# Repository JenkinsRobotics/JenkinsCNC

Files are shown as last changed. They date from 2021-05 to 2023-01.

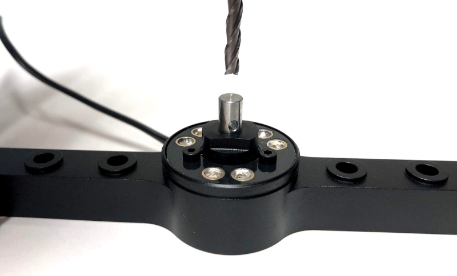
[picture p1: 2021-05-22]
CODE/SDCARD/www/img/touchplate.201649f8.png

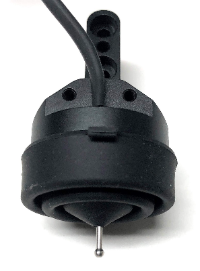
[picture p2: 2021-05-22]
CODE/SDCARD/www/img/probe.2c0976e9.png

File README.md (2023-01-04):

## Jenkins Robotics
# Jenkins CNC Project Files
<!-- This is commented out. -->

## Project Information

Project Status : <mark style="background-color: green"> &nbsp; COMPLETED &nbsp;</mark>  
Code Status : <mark style="background-color: green"> &nbsp; GOOD &nbsp;</mark>  
Development Status : <mark style="background-color: red"> &nbsp; NOT ACTIVE &nbsp;</mark>  

&nbsp;
## General Information

 This is the project files for our Shapeoko 3 xxl. Our goal is to make our shapeoko 3 as automated as possible. To achive this goal we have installed multiple upgrades onto our cnc including: 
- [x] Duet 3 Control Board
- [x] Pnumatic tool changer
- [x] Varible Fequency Drive & spindle
- [x] Tool TCP Probe
- [x] Work Piece XYZ Probe
- [x] Custum Fusion 360 Post Processor
- [x] Pnumatic Dust Shoe

&nbsp;
## WATCH NOW ON YOUTUBE

 Watch the project playlist on youtube. 

 &nbsp;

image alt text (https://youtube.com/playlist?list=PLNTKXZ4hgP_jekZOWw05JcJtyseCdSsIV "YouTube")

&nbsp;
## Support

Did this project help you? Consider supporting! 

Consider Subscribing: https://bit.ly/2DgZyuq <br>
Patreon ➔ https://www.patreon.com/JenkinsRobotics <br>
Venmo ➔ https://venmo.com/u/JenkinsRobotics <br>

&nbsp;
## Table of Contents

**[Project File Structure](#project-file-structure)**<br>
**[Installation Instructions](#installation-instructions)**<br>
**[Next Steps](#next-steps)**<br>
**[Components](#components)**<br>
**[Notes and Miscellaneous](#notes-and-miscellaneous)**<br>
**[Links](#links)**<br>

&nbsp;
## Project File Structure

The following is a breakdown of the different folders and the files contained in them:

1. **CAD**
   - *Online Models*
    Reference CAD models were used in the modeling of the shapeoko 360. Including a generic Shapeoko 3 model and a Duet 3 Model. We are also using a generic CAD cover for the LCD screen that can be downloaded directly from thingiverse. All reference CAD models used are copied here with any other documentation and licenses that came with the file. 

   - *Jenkins Robotics CAD*
    All released CAD models will be posted here on Github. Every CAD model made by us are given a part number (JRCNC###). Original files are created using fusion 360. Most files will also be given proper engineering drawings once a release version of the file is posted.
    
    &nbsp;
2. **CODE**  
   - *SDCARD*
    This folder contains a copy of all they files located on our Duet 3 Motherboard SD Card. The system drive contains multiple subfolders each containing different gcode / system files. Before Copying/referencing our  custom files it is best to upgrade the stock firmware and system files. The official Duet 3 releases can be found on GitHub.  [RepRap Files](https://github.com/Duet3D "Duet3D").
      
   - *Macros*
    The Macro folder contains all the additional system files needed for the Duet 3. Files are grouped by their function. 
     **Directions:**
        - Upload any of the desired files. Then review the files and make any necessary  adjustment to the position points and the probe/sensors numbers.  

   - *Sys*
    The System folder contains all the important system files needed for the Duet 3. Each file serves as important gcode files that configures the machine and provide necessary gcode for specific processes like tool changes. 
        **Directions:**
        - Upload the following files: Config*, TFree, Tpost, Tpre, Zprobe, Lighthome, lighton. 
        - Config file is specific to each machine. and will require modification based on the wiring of your specific machine. Use our config file and our wire diagram as reference. 
        - The TFree/Tpost/Tpre and ZProbe are all required files to add support for ATC and Automatic Tool offset probe. Copy these files and adjust the position data as necessary. 

    &nbsp;
3. **DIAGRAMS**
   - *Jenkinc CNC Wire Diagram (JRCNCWD1)*
    A wiring diagram is a simplified conventional pictorial representation of an electrical circuit. It shows the components of the circuit as simplified shapes, and the power and signal connections between the devices Reference the wire diagram to review how each electrical component is connected to the Duet board

   - *Duet 3 Reference files*
    Reference files are used to highlight specific information that useful for the operation, installation of the duet board.  Duet3D online wiki contains many more useful information and [Documentations](https://duet3d.dozuki.com/ "Duet3D").
  
    &nbsp;
4. **FUSION 360 POST PROCESSOR**
     
   - *JenkinsCNCReprap.cps*
    A post processor is the link between the CAM system and your CNC machine. The Post Processor translated the CAM instruction including information like the toolpath data, the type of operation, and the desired spindle feeds/speeds into the language that a CNC machine understands (gcode). Despite the fact that the DUET 3 runs RepRap Firmware, the standard RepRap post processor do not work for CNC machining. Our Custom post processor is based on the default RepRap post processor but fixes the gcode syntax errors and adds  Automatic Tool Change / Spindle Controls support. 
    **Directions:**
      - Uploading file to Fusion 360 Cloud Storage [Personal-cloud]
        With-in Fusion 360 open the project navigation panel. Under Libraries select "Assets", then select folder "CAMPosts" (if no folder exist then create one.) Upload the custom Post Processor within this folder for cloud storage. 
      - Create NC Program
        After creating your CAD model select the "Manufacturing Tab" in Fusion 360. Complete the "Setup" process and the desired toolpaths. Create a new "NC Program".  Under "Post Configuration / Library" specify the location of the Post Processor File [personal-cloud recommended]. Under Post specify the desired file "Jenkins CNC RepRap". Adjust Post Properties if desired, then export gcode.  

    &nbsp;
5. **MANUALS**
   - *Reference Materials*
    The manuals folder contains reference material for different hadware apart of the CNC. 
      - The VFD Manual contains the custom settings specific for our spindle.
      - Automatic Tool Changer (ATC) manual contains information required to "run-in" a new spindle to properly prepare it before running production

> Note: Updating the RepRap firmware should be done carefully. Uploading the updated ZIP file could erase custom gcode files. 

&nbsp;
## Installation Instructions

Installation instructions can be found in the youtube video linked below 

 ### Video link  be updated soon

image alt text (https://youtube.com/playlist?list=PLNTKXZ4hgP_jekZOWw05JcJtyseCdSsIV "YouTube")

<!-- This is commented out.  

The following is a breakdown of the different folders and the files contained in them:

```
cd utils
node build.js
```

Create a file with a `.zip` extension containing these files and directories:

```
manifest.json
common/
chrome/
```

Create a file with a `.xpi` extension containing these files and directories:

```
chrome.manifest
install.rdf
common/
firefox/
```

 This is commented out. -->

&nbsp;
## Next Steps

This project is now completed. No next steps are planned. We can release bug fixes if found. 

If you require assistant join our discord channel linked down below.

&nbsp;
## Components 

The following is a breakdown of key components for this project:
&nbsp;
| Item | Function | Cost  | Link  |
| --- |:---:| -----:|-----:|
| Fusion 360 | CAD | Free | Free |
| VS Code | Text Editor | Free | Free |
| Spindle | Spindle  | $220 | (https://www.amazon.com/dp/B088824MPT/...) |
| Tool Changer for Water or Air Cooled Spindle 0.8 or 1.5KW 65mm | ATC | $400 | (https://cnccat.com/index.php?id=2&productid=1964&catid=0&subcatid=&lang=en) |

&nbsp;
## Notes and Miscellaneous

Disclaimer :
Modifying your Shapeoko  will void the warranty. Do at your own risk.

**ENJOY!!**

That’s  all Folks. Hope this can help you in some way.
... Consider Supporting Us Down Below. 

&nbsp;
## Links

SUPPORT US ► 

Consider Subscribing: https://bit.ly/2DgZyuq <br>
Patreon ➔ https://www.patreon.com/JenkinsRobotics  <br>
Venmo ➔ https://venmo.com/u/JenkinsRobotics <br>

FOLLOW US ►

Discord ➔ https://discord.gg/sAnE5pRVyT <br>
Patreon ➔ https://www.patreon.com/JenkinsRobotics <br>
Twitter ➔ https://twitter.com/j <br>
Instagram  ➔ https://www.instagram.com/jenkinsrobotics/ <br>
Facebook ➔ https://www.facebook.com/jenkinsrobotics/  <br>
GitHub  ➔ https://jenkinsrobotics.github.io <br>

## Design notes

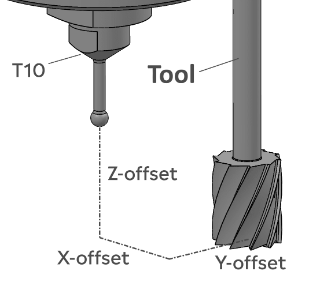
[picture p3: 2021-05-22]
CODE/SDCARD/www/img/tooloffset.c75178cf 2.png

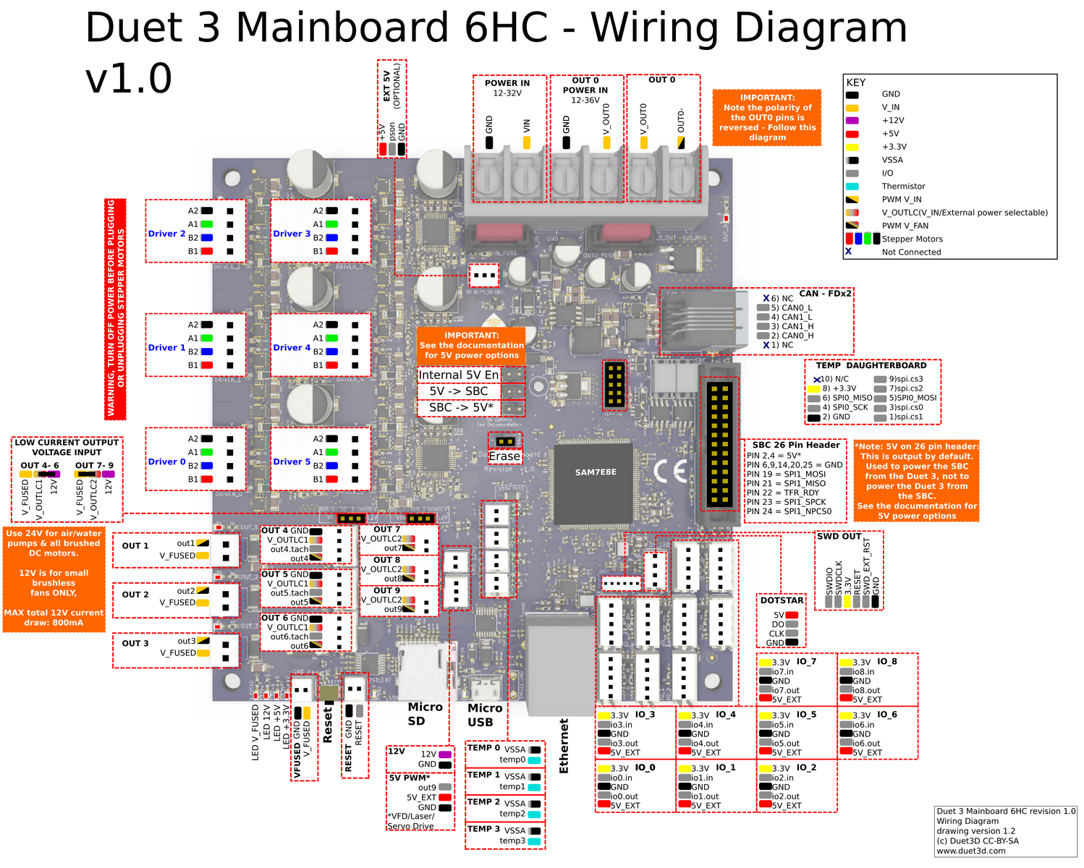
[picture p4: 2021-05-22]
DIAGRAMS/DUET 3 Diagram.jpg

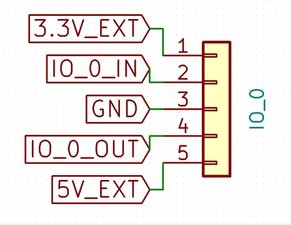
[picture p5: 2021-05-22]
DIAGRAMS/Duet 3 IO port.jpg

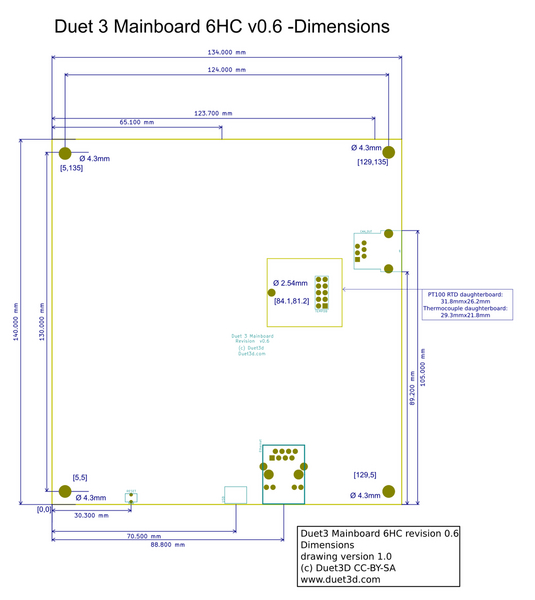
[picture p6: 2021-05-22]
DIAGRAMS/DUET 3 BOARD SIZE.jpg

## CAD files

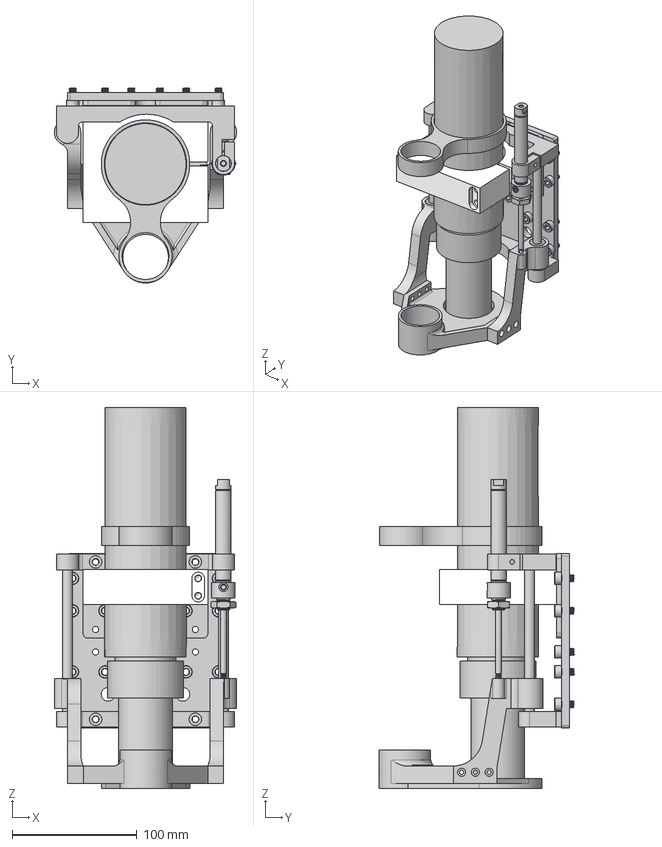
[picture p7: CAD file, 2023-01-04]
CAD/JR ASSEMBLIES/shapeoko Z Axis Upgrades v40.step
146.3 x 156.4 x 305.5 mm
91290A316 x 14
Shapeoko3_Spindle_Mount
LM8UU x 2
rod x 2
6498K122
ATC
spindle
JRCNC0013
JRCNC0011
JRCNC0014
JRCNC0015
JRCNC0016
JRCNC0014-2
JRCNC0007

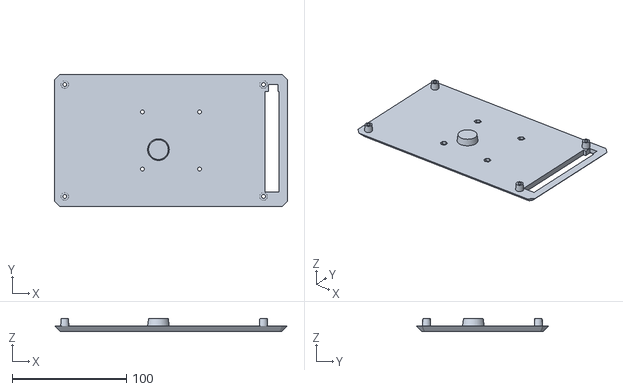
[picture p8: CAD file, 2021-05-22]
CAD/PanelDue_7i_case_thin/files/PanelDue7iBack.stl
204.0 x 116.0 x 11.3

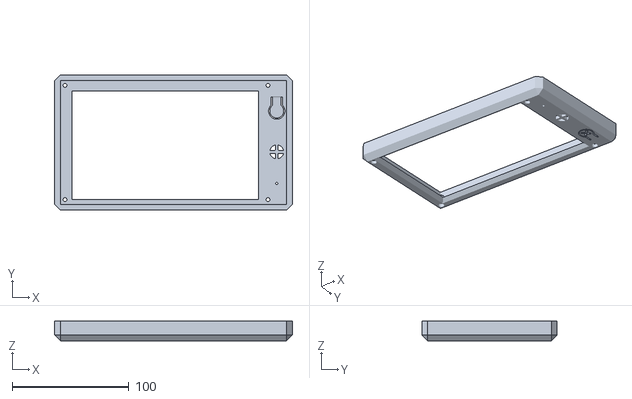
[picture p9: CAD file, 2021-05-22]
CAD/PanelDue_7i_case_thin/files/PanelDue7iFront.stl
204.0 x 116.0 x 16.7

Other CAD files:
DIAGRAMS/DUET CNC 3.0.dwg
DIAGRAMS/JRCNCWD1.dwg
DIAGRAMS/DUET CNC 2.0.dwg
CAD/JRCNC0001 v12.f3d
CAD/JRCNC0002 v2.f3d
CAD/JRCNC0006 v3.f3d
CAD/JRCNC0007 v3.f3d
CAD/JRCNC0008 v3.f3d
CAD/JRCNC0009 v3.f3d
CAD/JRCNC0010 v28.f3d
CAD/JRCNC0011 v29.f3d
CAD/JRCNC0012 v8.f3d
CAD/JRCNC0013 v21.f3d
CAD/JRCNC0014 MIRROR v4.f3d
CAD/JRCNC0014 v32.f3d
CAD/JRCNC0014-2 v4.f3d
CAD/JRCNC0015 v7.f3d
CAD/JRCNC0016 v16.f3d
CAD/JRCNC003 v11.f3d

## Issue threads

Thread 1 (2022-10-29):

cad/shapeoko Z Axis Upgrades is not opennable

chernogorsky, 2022-10-29:
Hi, file
[shapeoko Z Axis Upgrades](https://github.com/JenkinsRobotics/JenkinsCNC/blob/master/CAD/JR%20ASSEMBLIES/shapeoko%20Z%20Axis%20Upgrades) is
is not oppenable

P.S. trying to make ATC with shoe.
D3, but PrintNC instead of Shapeoko

jonjenkins31, 2023-01-04:
I Have fixed the file

Closed 2023-01-04.

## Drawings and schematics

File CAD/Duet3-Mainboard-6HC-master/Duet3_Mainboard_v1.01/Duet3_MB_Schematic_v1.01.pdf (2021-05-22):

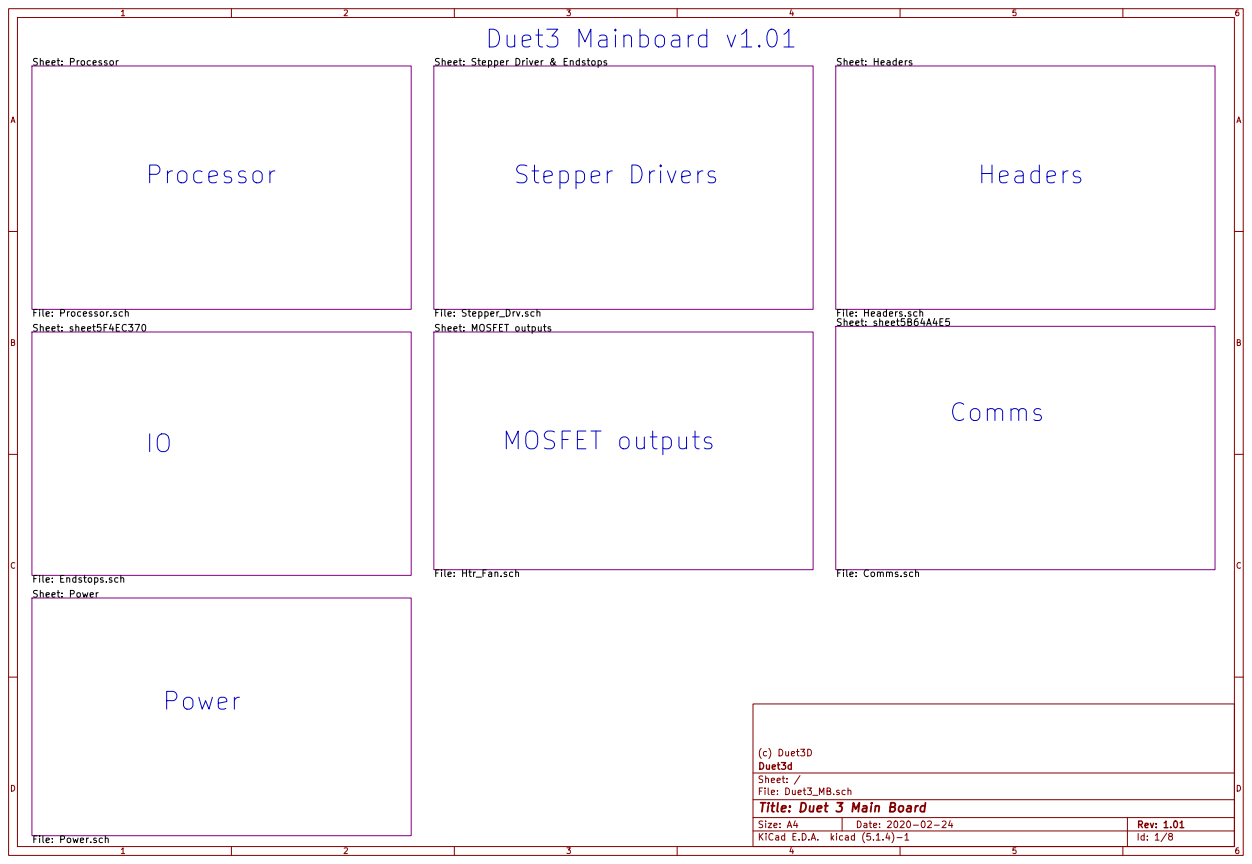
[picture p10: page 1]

Sheet: Headers File: Headers.sch Sheet: Power File: Power.sch

Sheet: Stepper Driver & Endstops

Id: 1/8 Title: Duet 3 Main Board

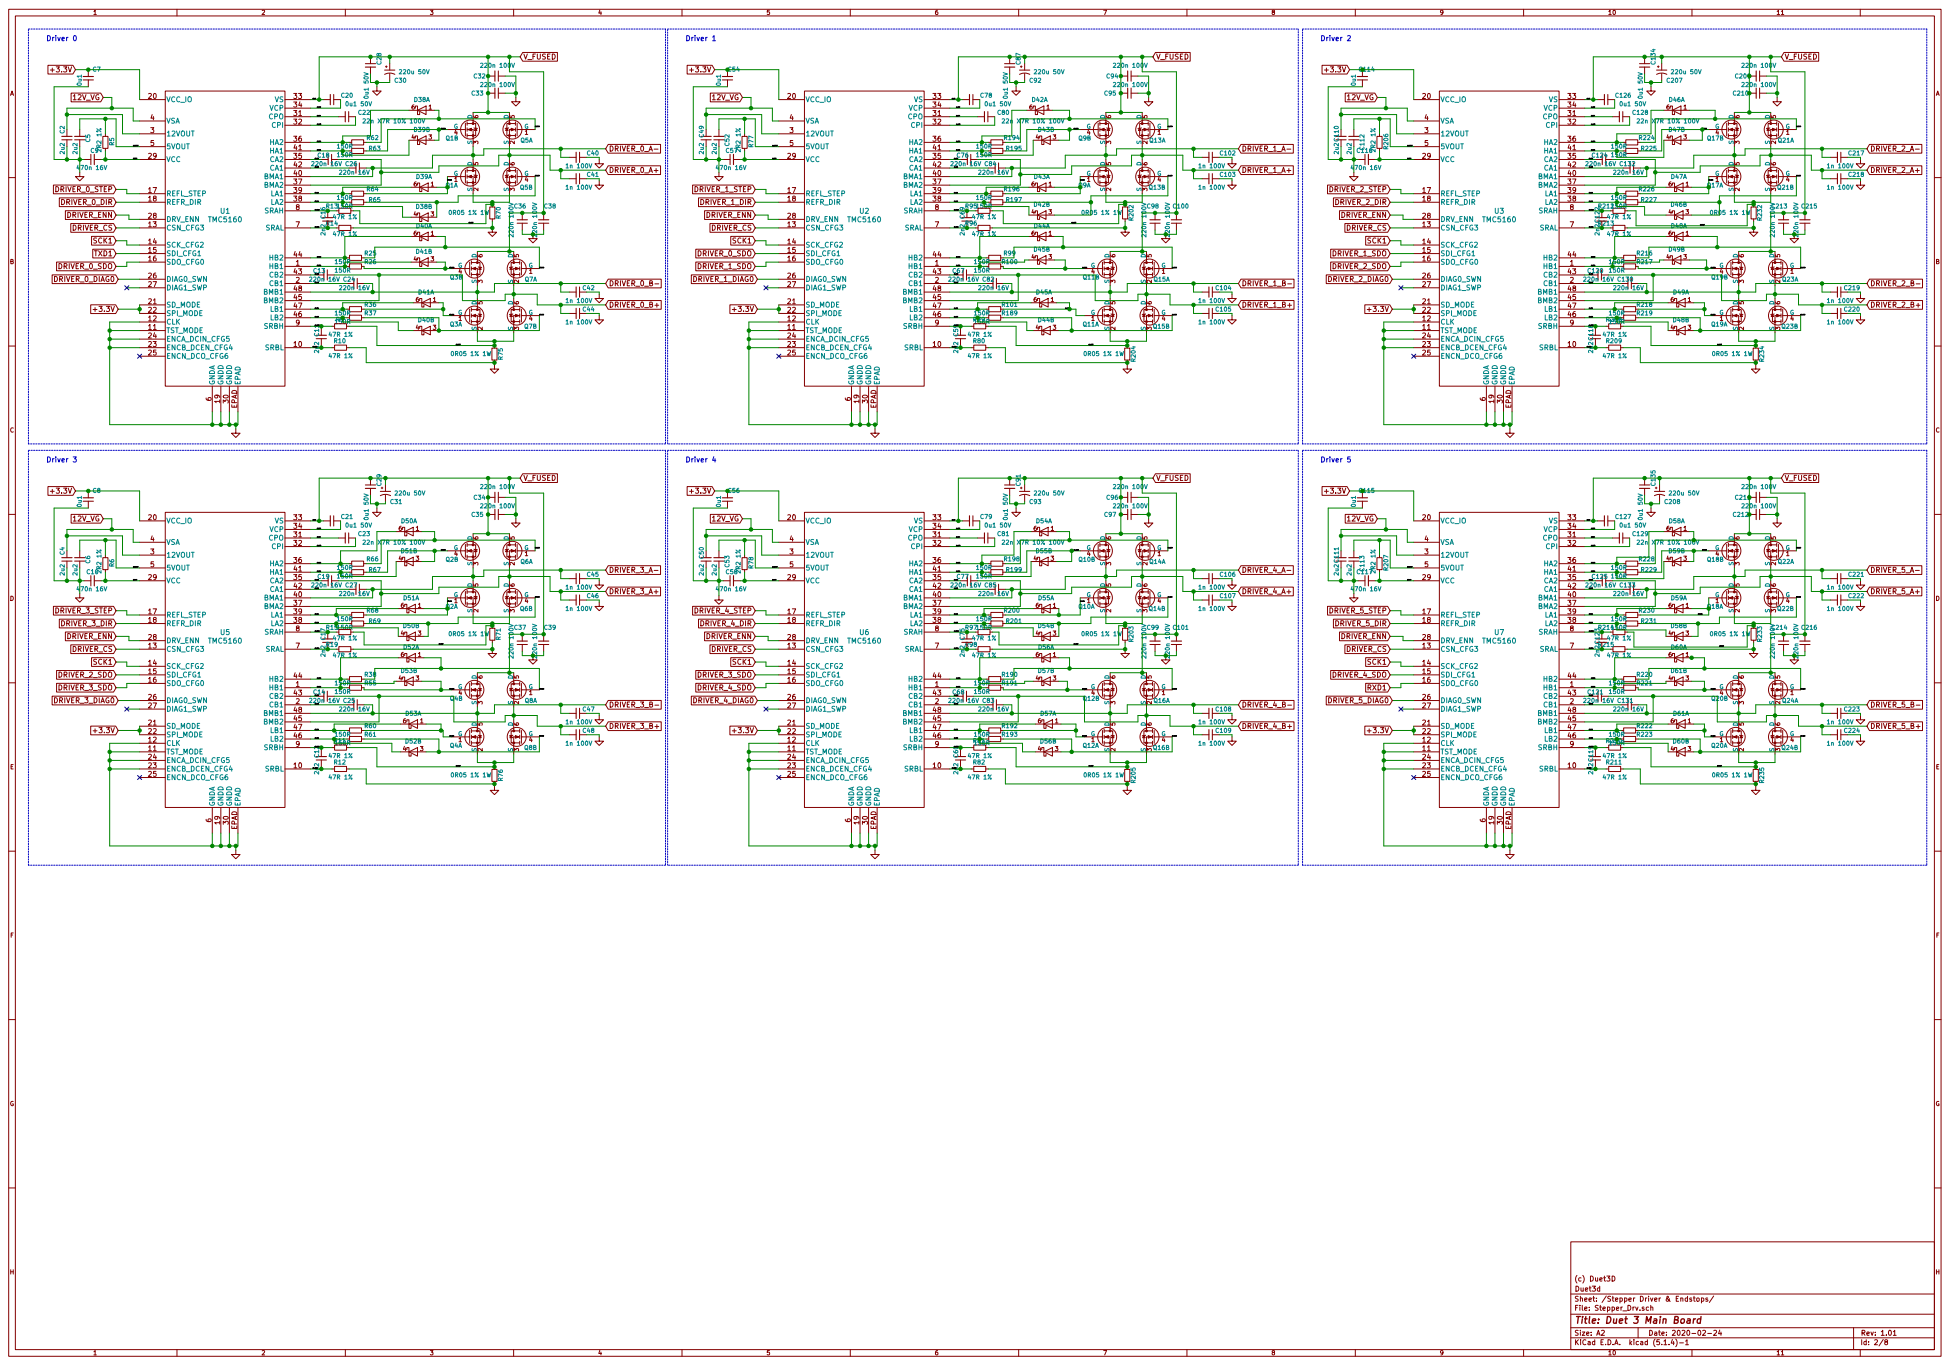
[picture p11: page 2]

6 SRAL 7 SRAH 8 SRBH 9 EPAD EPAD U2 TMC5160 C78

6 SRAL 7 SRAH 8 SRBH 9 EPAD EPAD U1 TMC5160 C5 2u2 C9

5 Q9A HB1 1 SRBL 10 TST_MODE 11 CLK 12 CSN_CFG3 13 SCK_CFG2 14 SDI_CFG1 15 SDO_CFG0 16 REFL_STEP 17 REFR_DIR 18 GNDD 19 CB1 2 VCC_IO 20 SD_MODE 21 SPI_MODE 22 ENCB_DCEN_CFG4 23 ENCA_DCIN_CFG5 24 ENCN_DCO_CFG6 25 DIAG0_SWN 26 DIAG1_SWP 27 DRV_ENN 28 VCC 29

6 SRAL 7 SRAH 8 SRBH 9 EPAD EPAD U6 TMC5160 C53 2u2 C58

6 SRAL 7 SRAH 8 SRBH 9 EPAD EPAD U5 TMC5160

(c) Duet3D
Sheet: /Stepper Driver & Endstops/ Duet3d

File: Stepper_Drv.sch
Id: 2/8 Title: Duet 3 Main Board

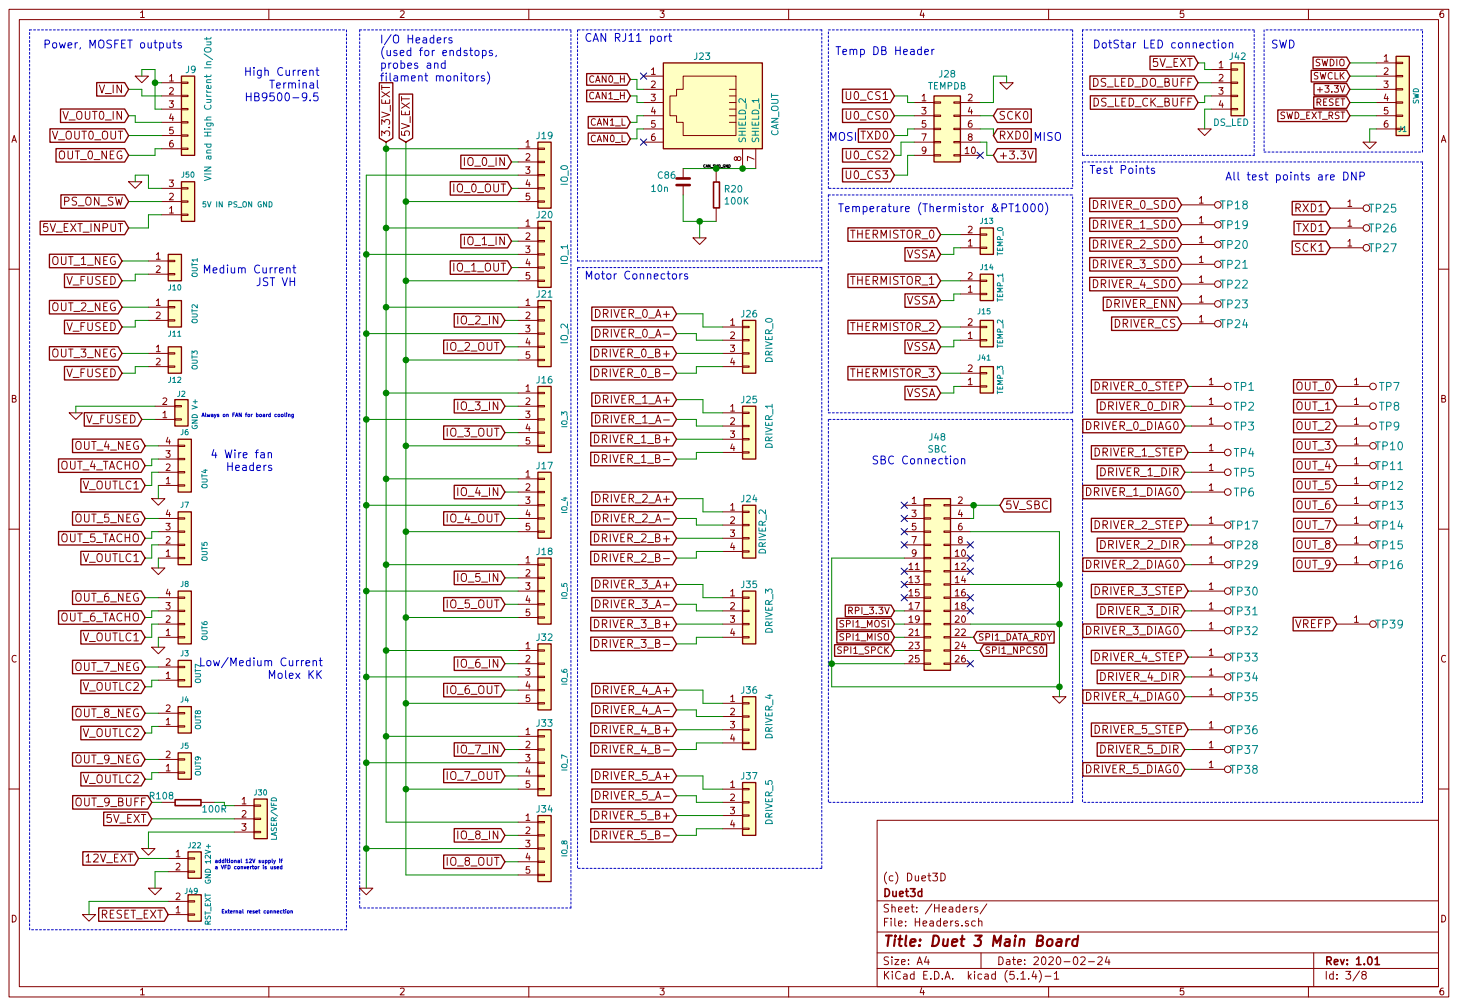
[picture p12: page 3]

Test Points High Current Terminal HB9500-9.5 Power, MOSFET outputs

Temp DB Header 4 Wire fan Headers

Always on FAN for board cooling

additional 12V supply if a VFD convertor is used

(c) Duet3D
File: Headers.sch Sheet: /Headers/ Duet3d

Id: 3/8 Title: Duet 3 Main Board

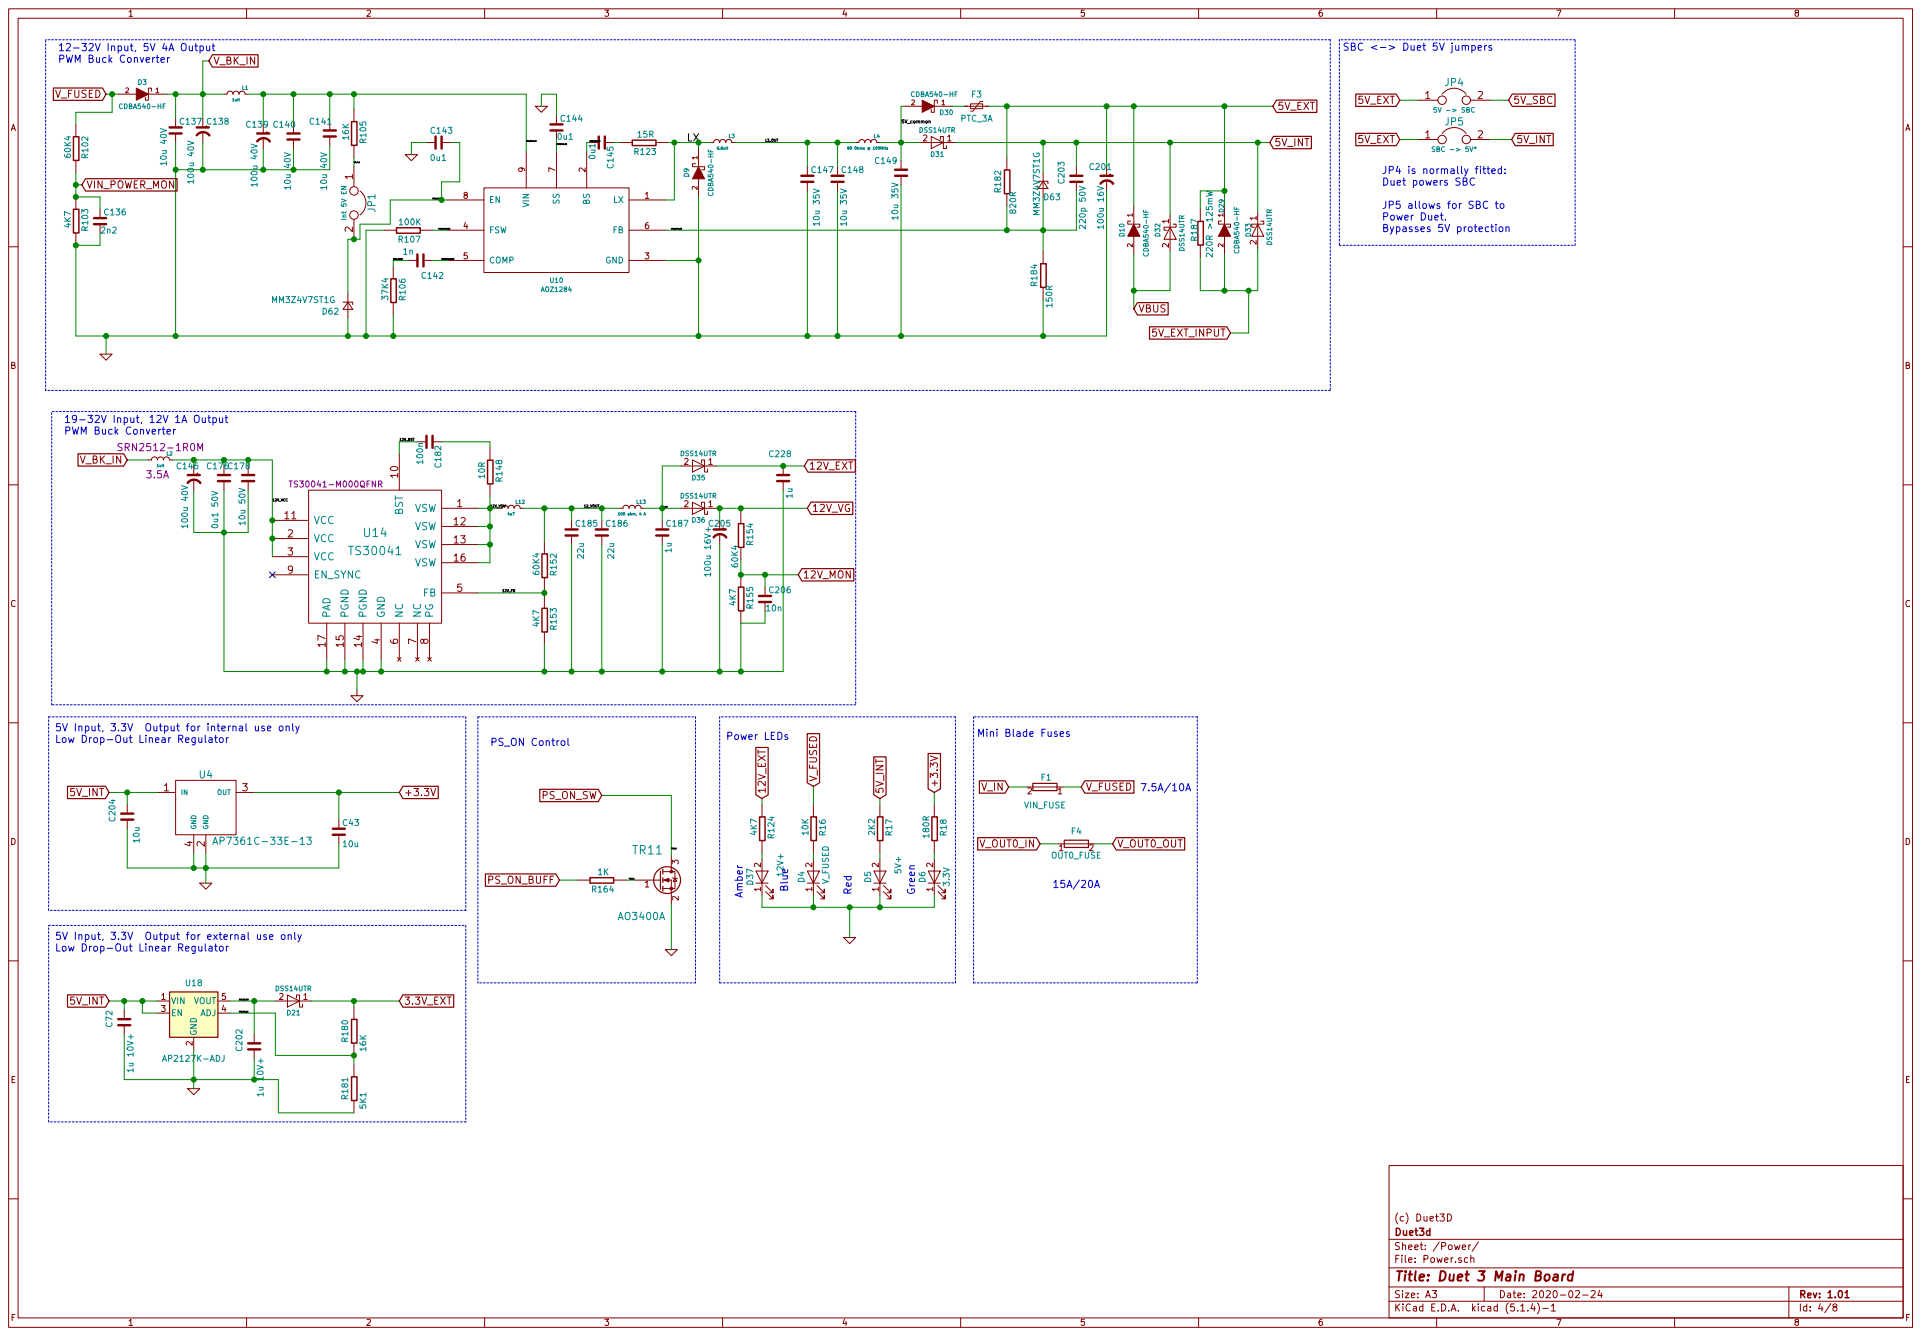
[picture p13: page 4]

2 GND 3 FSW 4 COMP 5 FB 6 SS

JP5 allows for SBC to Power Duet. Bypasses 5V protection

5V Input, 3.3V Output for internal use only

5V Input, 3.3V Output for external use only
Low Drop-Out Linear Regulator

2 EN 3 ADJ 4 VOUT 5 U18 AP2127K-ADJ

(c) Duet3D
File: Power.sch Sheet: /Power/ Duet3d

Id: 4/8 Title: Duet 3 Main Board

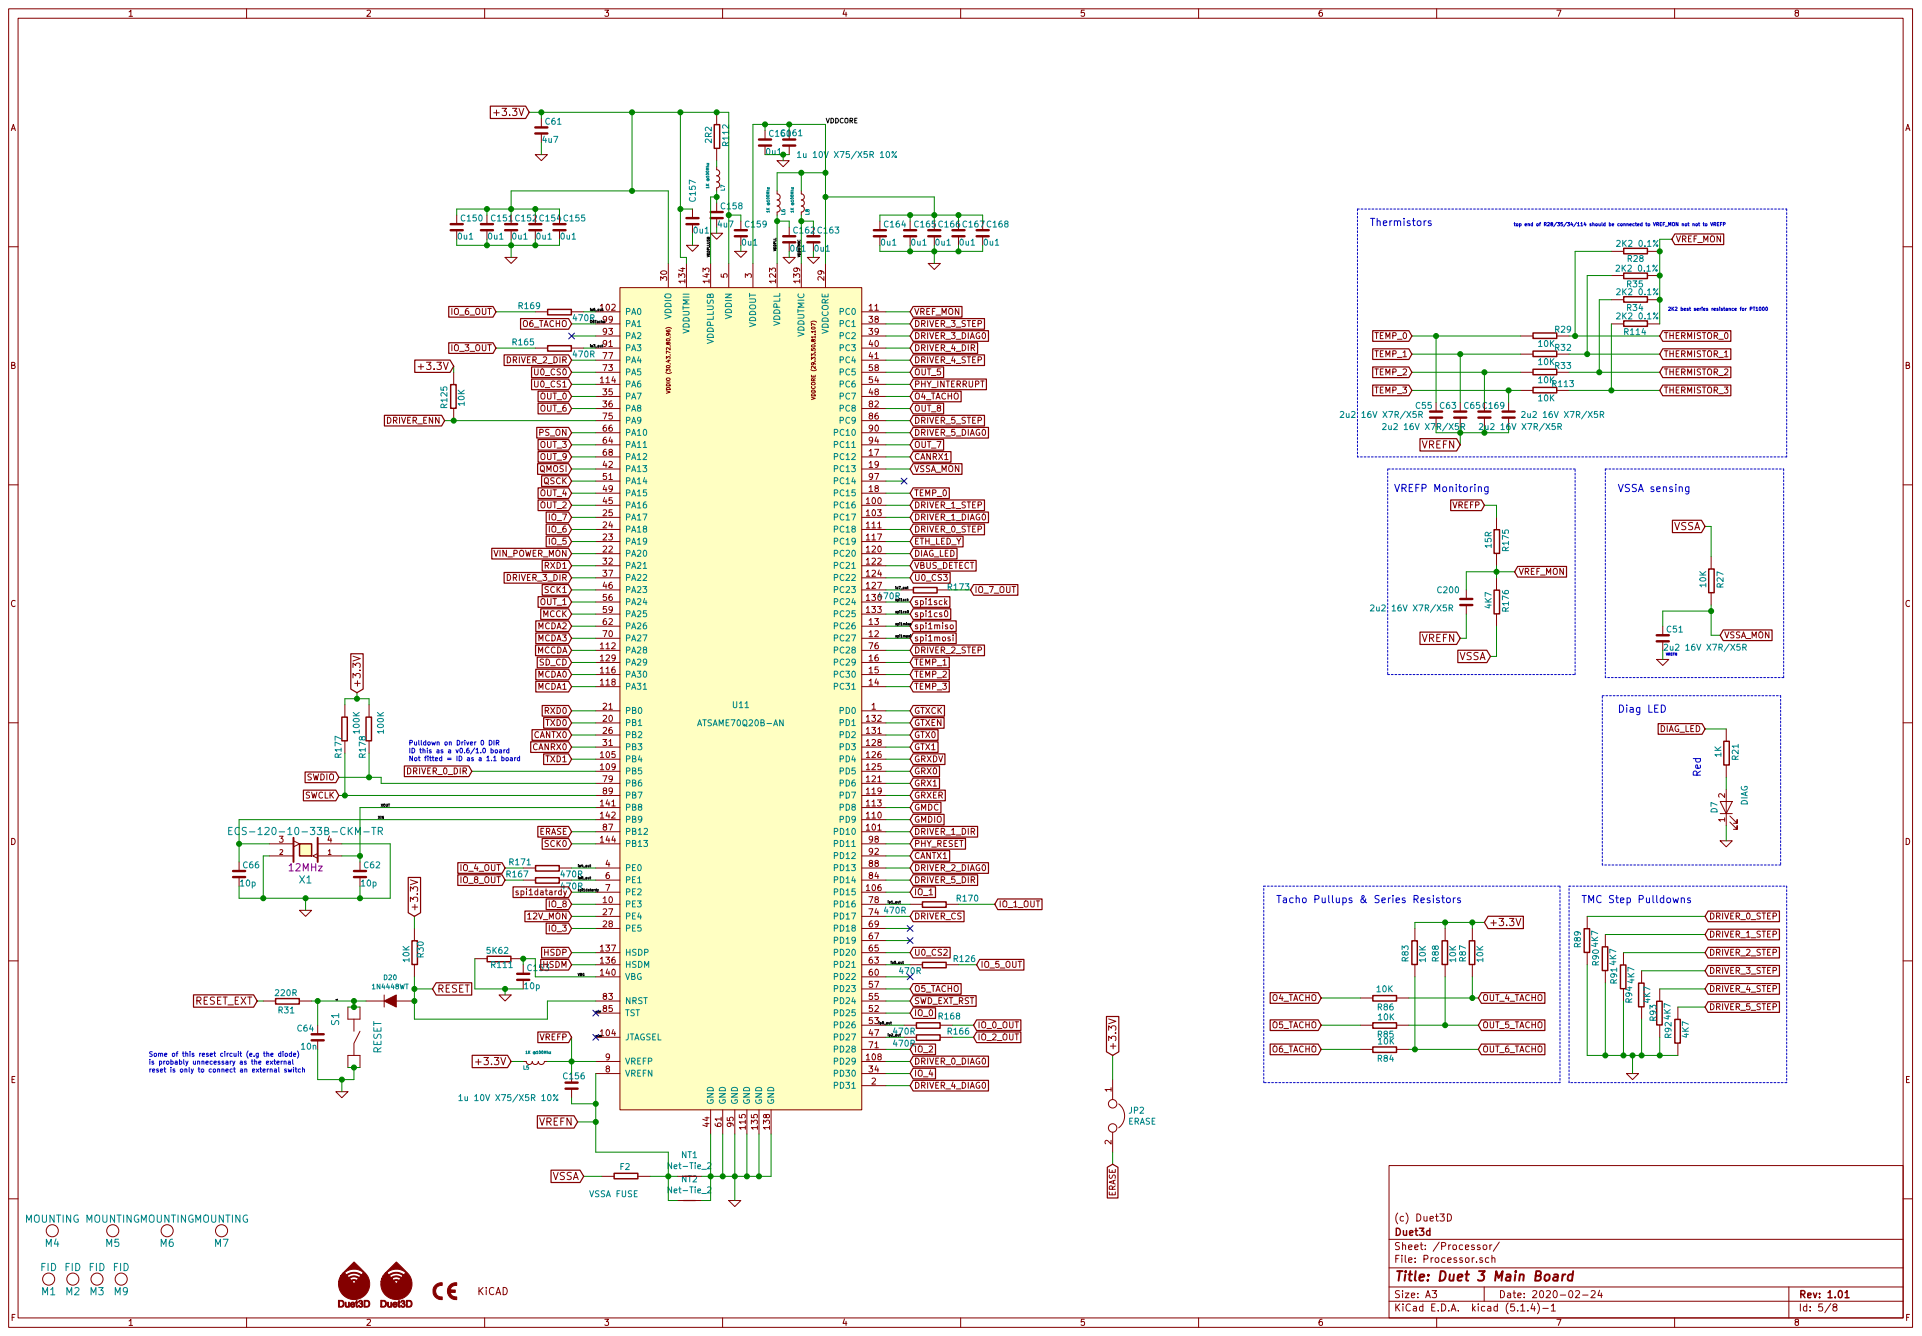
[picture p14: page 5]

top end of R28/35/34/114 should be connected to VREF_MON not not to VREFP
2K2 best series resistance for PT1000 Red

Pulldown on Driver 0 DIR

ID this as a v0.6/1.0 board Not fitted = ID as a 1.1 board Some of this reset circuit (e.g the diode)

Tacho Pullups & Series Resistors

is probably unnecessary as the external reset is only to connect an external switch

(c) Duet3D
File: Processor.sch Sheet: /Processor/ Duet3d

Id: 5/8 Title: Duet 3 Main Board

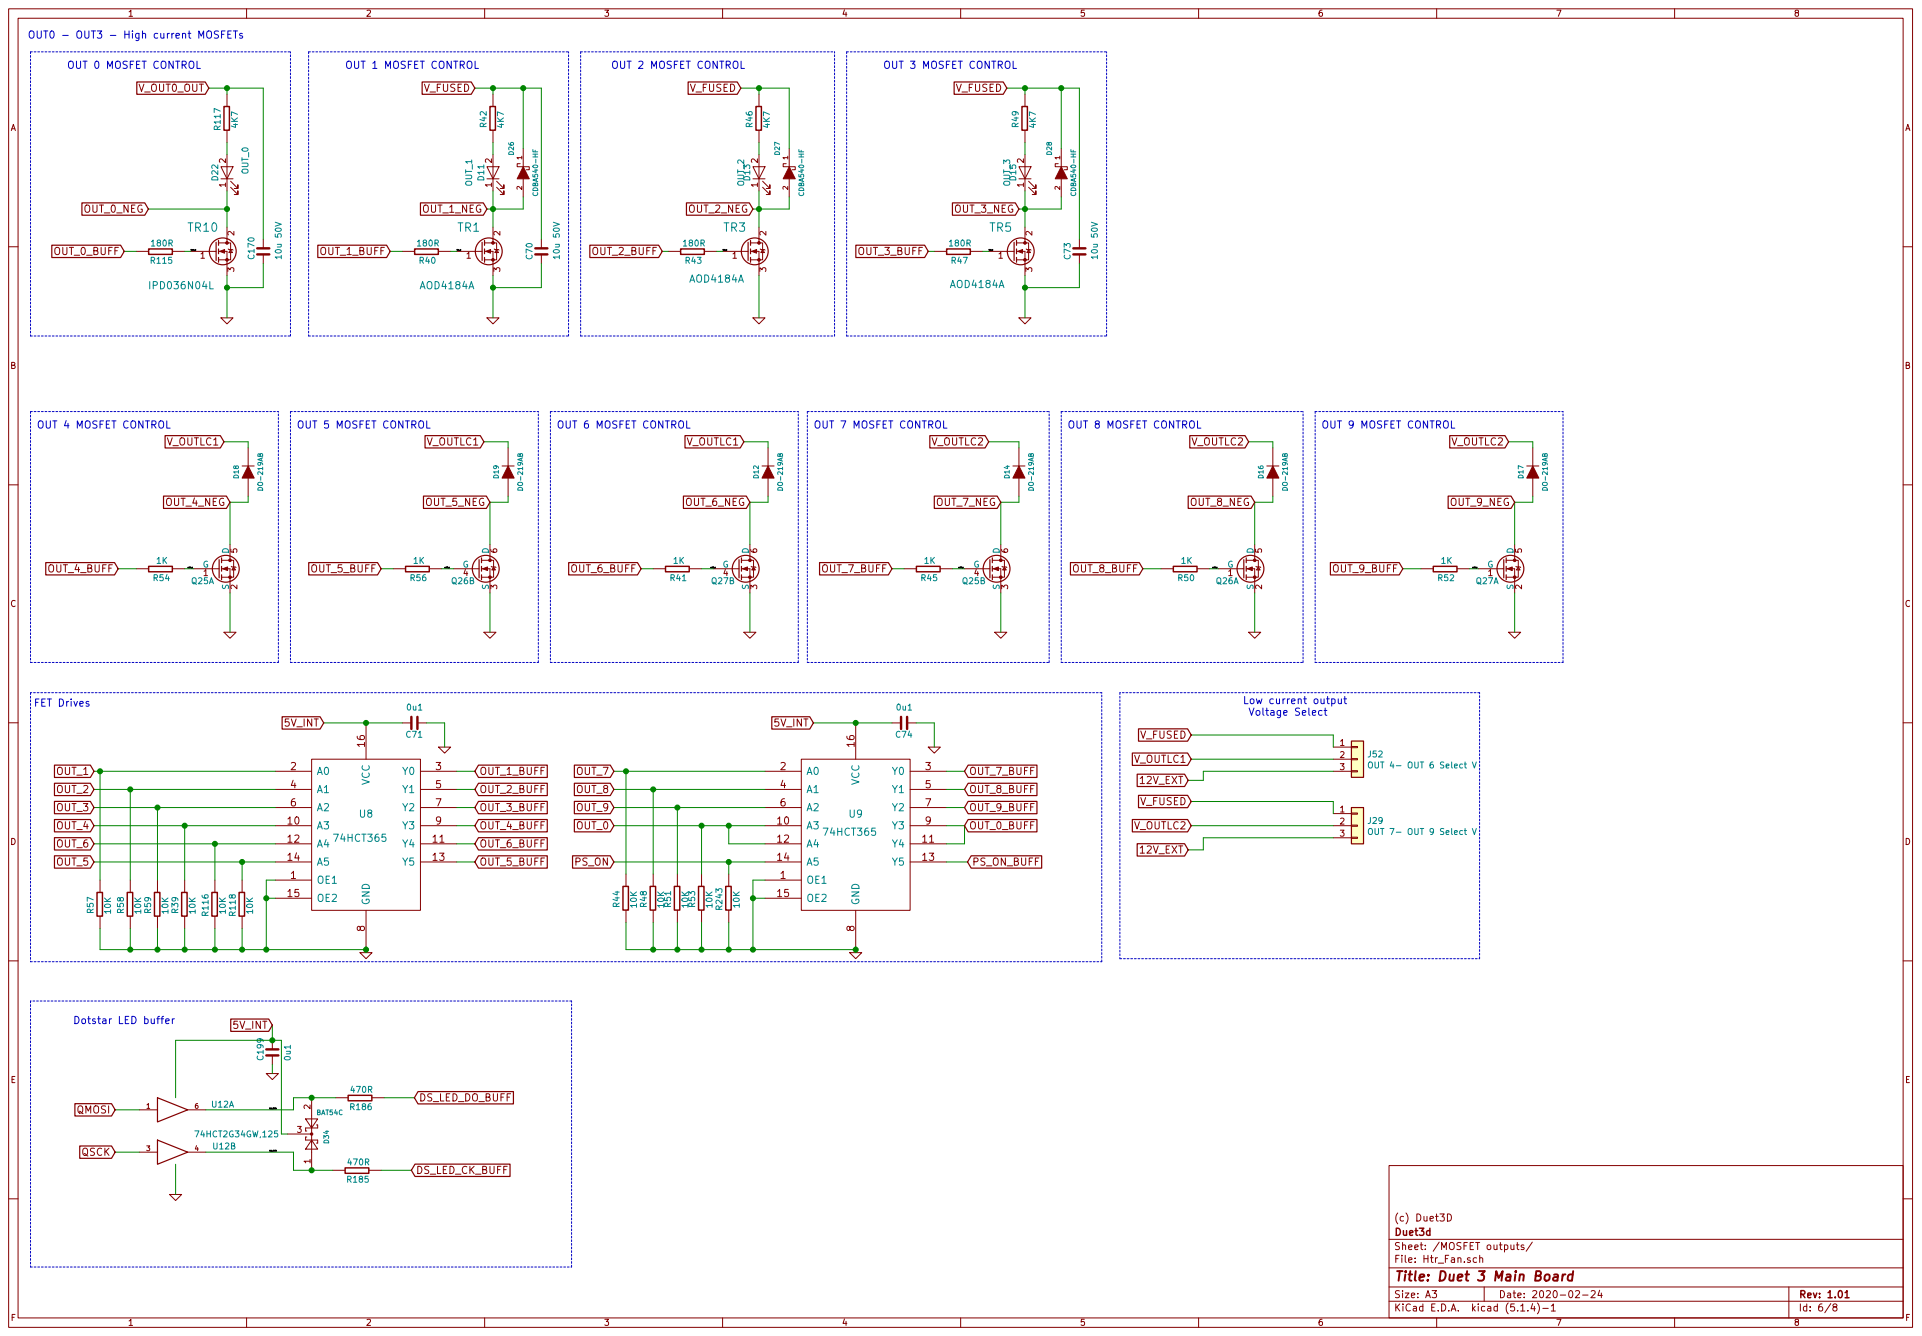
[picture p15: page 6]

File: Htr_Fan.sch
Id: 6/8 Title: Duet 3 Main Board

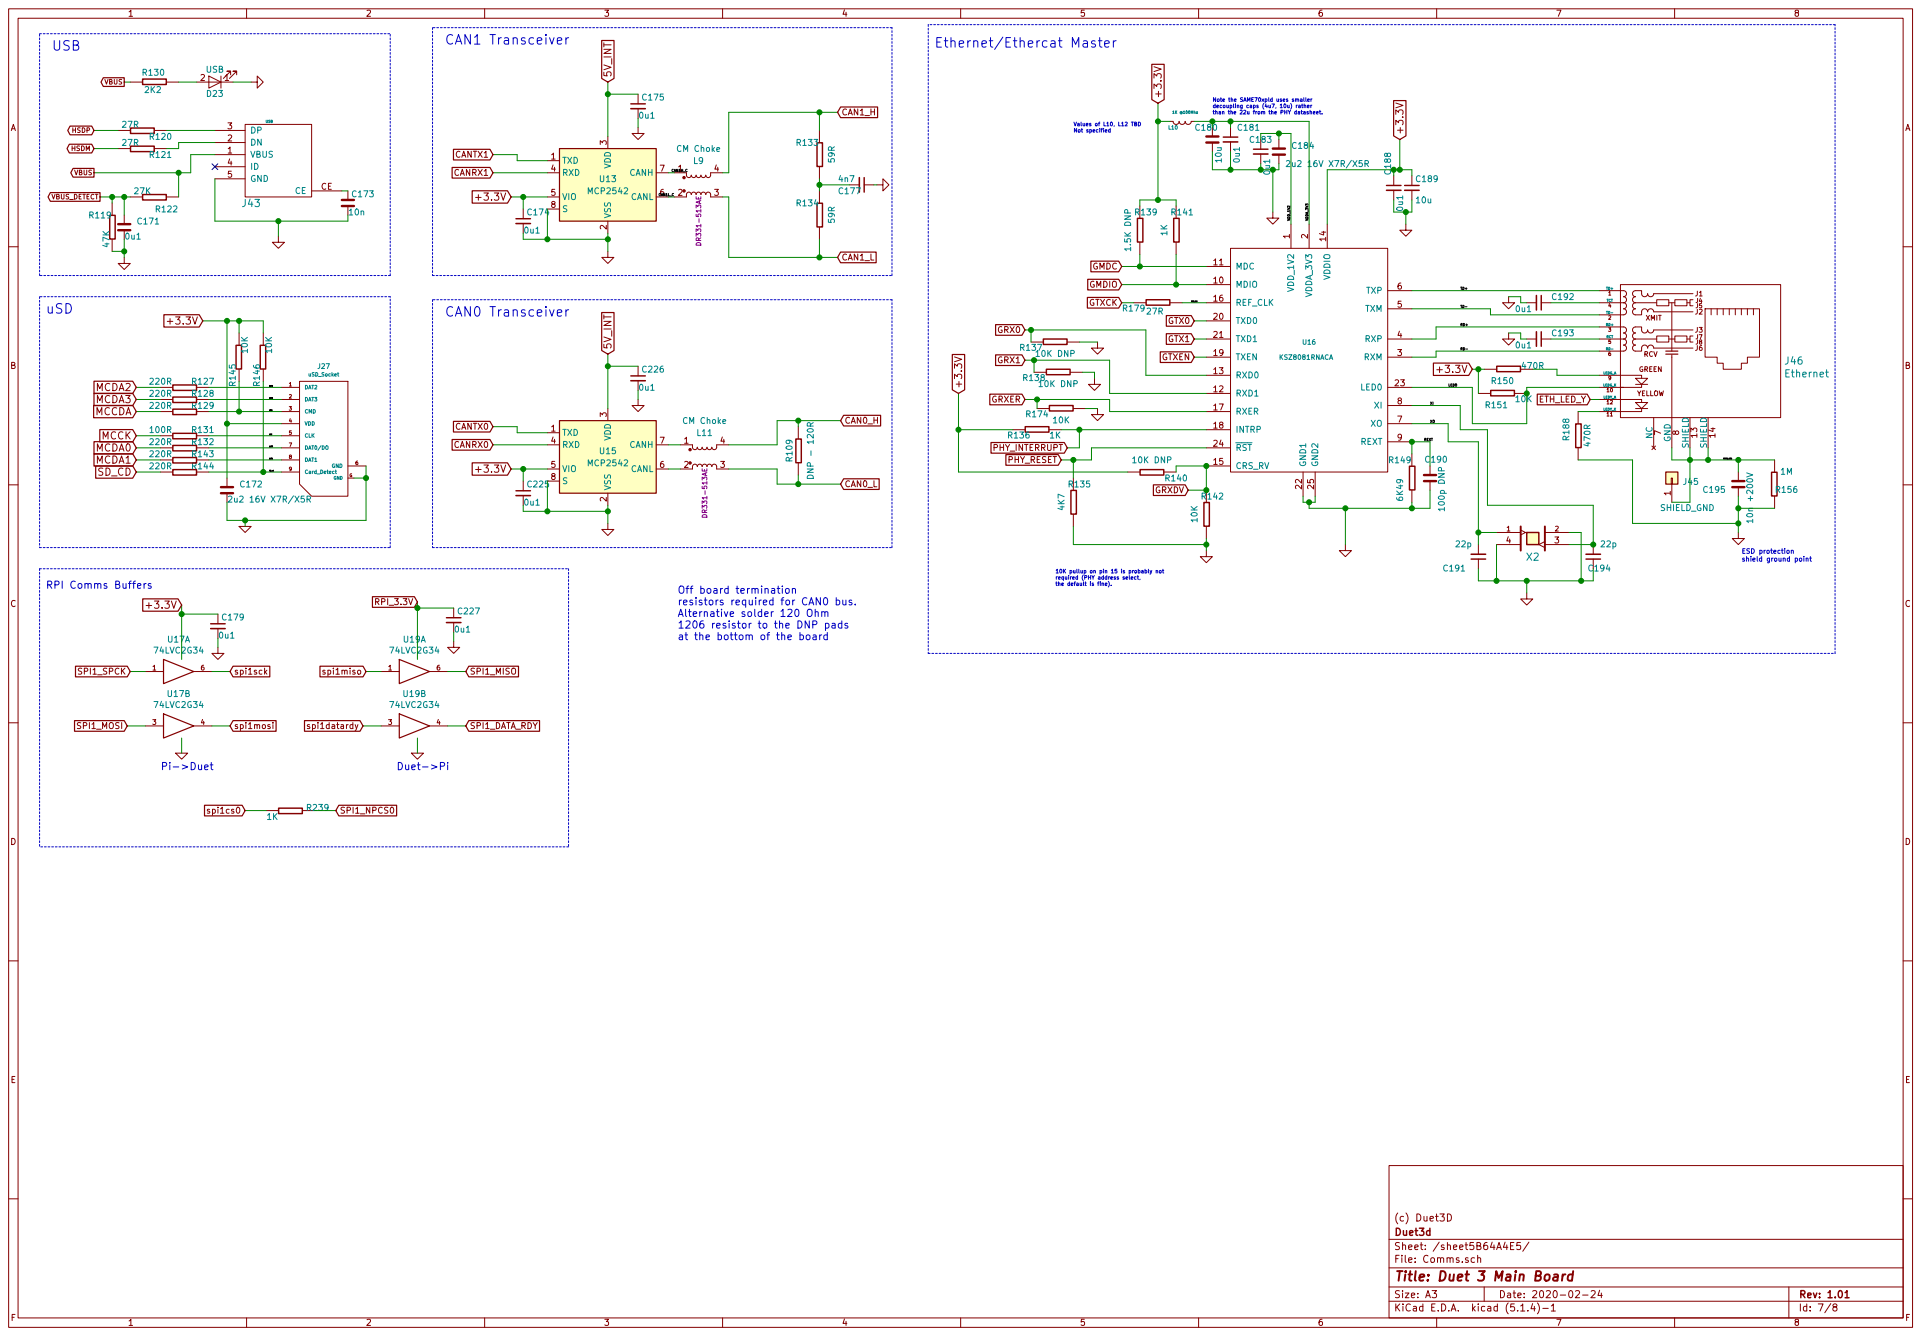
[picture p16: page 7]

CAN1 Transceiver

USB 2 2K2 | 1 D23 USB R121 USB R130

the default is fine). Ethernet/Ethercat Master

than the 22u from the PHY datasheet. Duet->Pi

3 RXD 4 VIO 5 CANL 6 CANH 7 S

1 MDIO 10 MDC 11 RXD1 12 RXD0 13 VDDIO 14 CRS_RV 15 REF_CLK 16 RXER 17

shield ground point uSD

10K pullup on pin 15 is probably not required (PHY address select,

Off board termination
resistors required for CAN0 bus.
Alternative solder 120 Ohm
1206 resistor to the DNP pads at the bottom of the board

(c) Duet3D
File: Comms.sch Sheet: /sheet5B64A4E5/ Duet3d

Id: 7/8 Title: Duet 3 Main Board

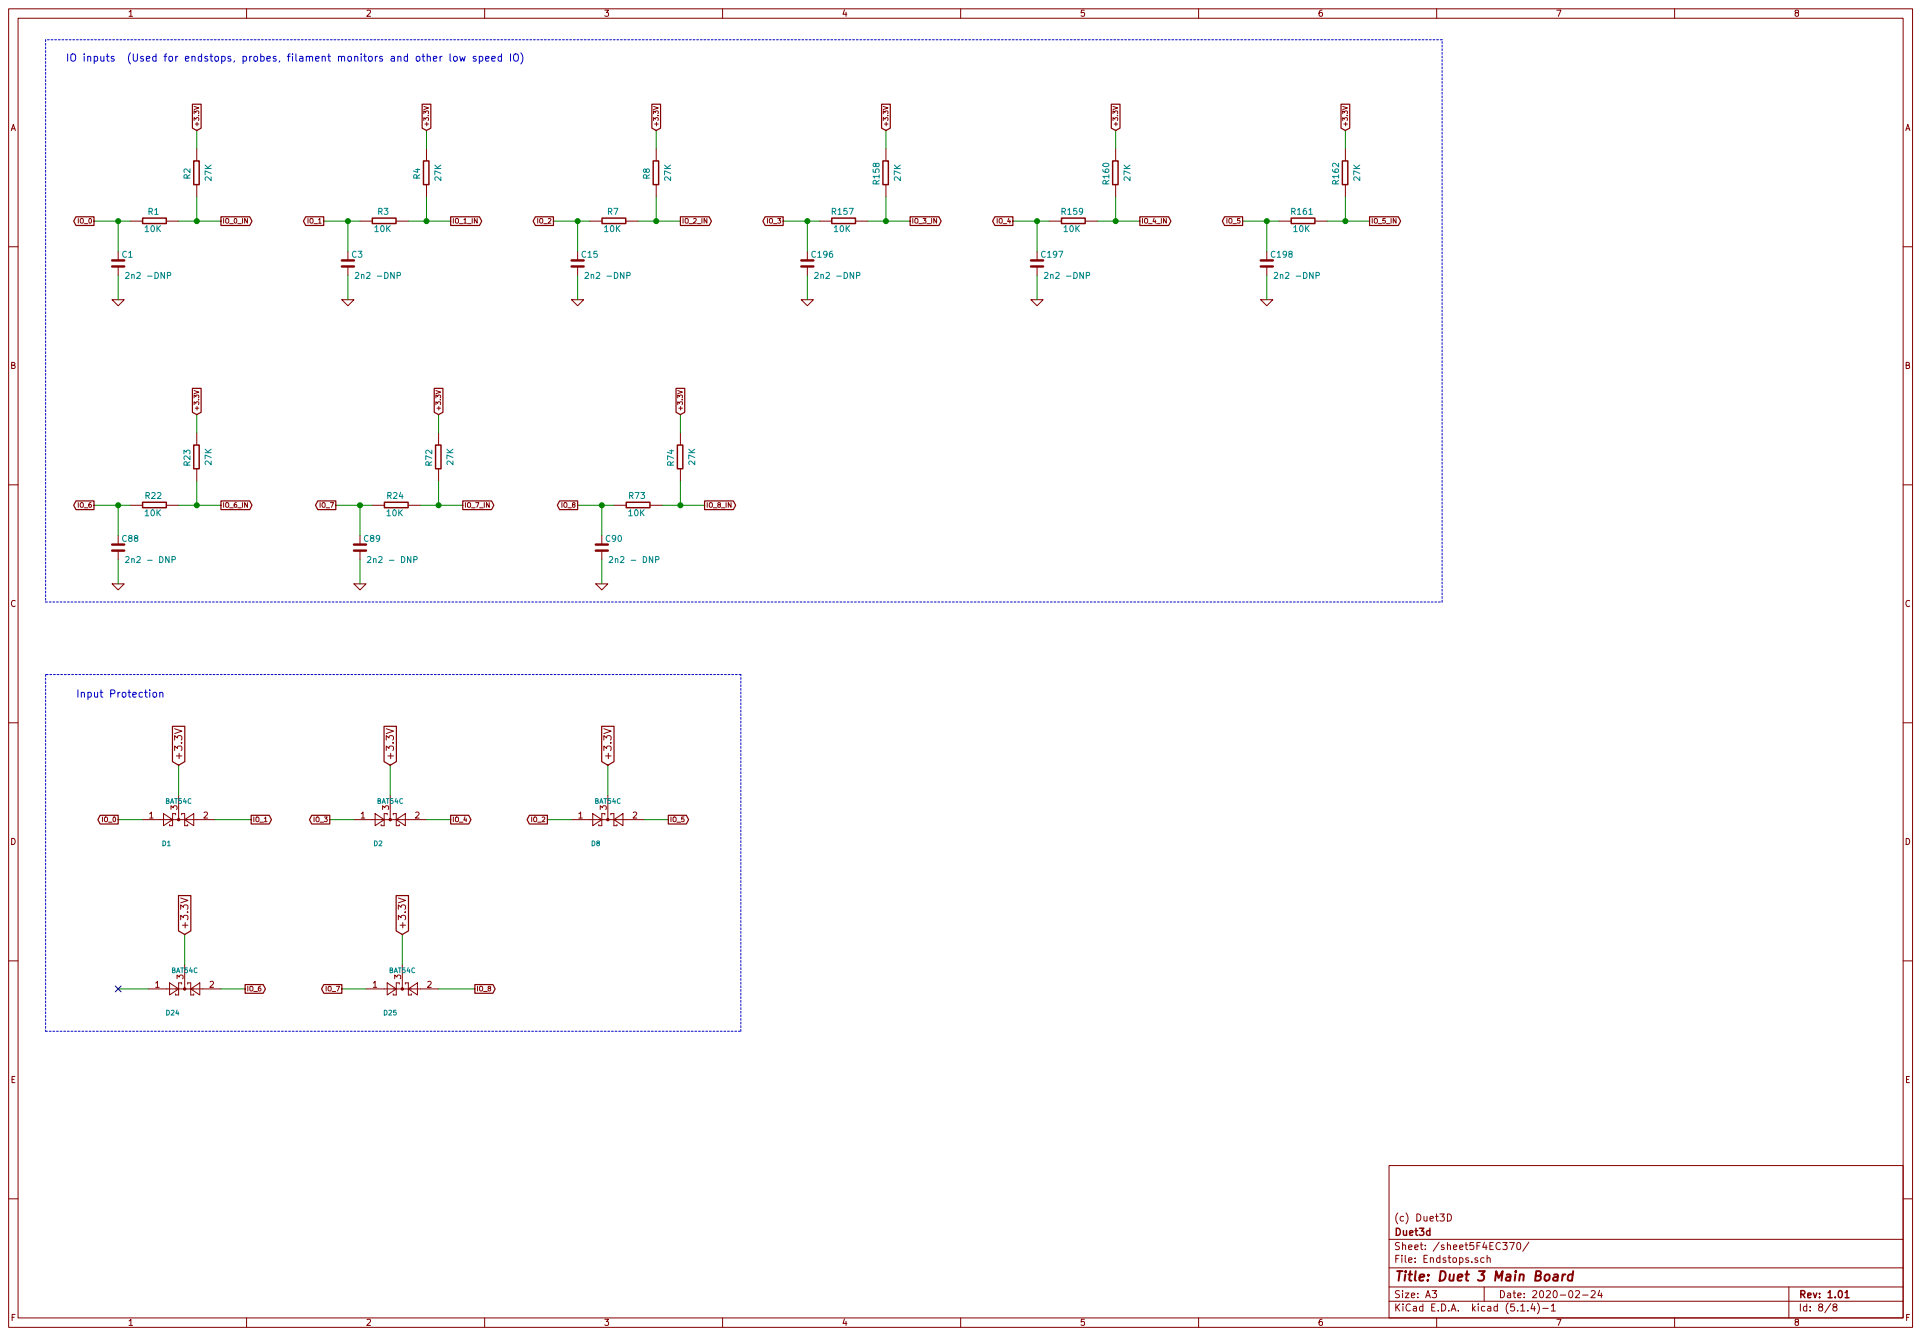
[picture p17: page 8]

IO inputs (Used for endstops, probes, filament monitors and other low speed IO)

(c) Duet3D
File: Endstops.sch Sheet: /sheet5F4EC370/ Duet3d

Id: 8/8 Title: Duet 3 Main Board

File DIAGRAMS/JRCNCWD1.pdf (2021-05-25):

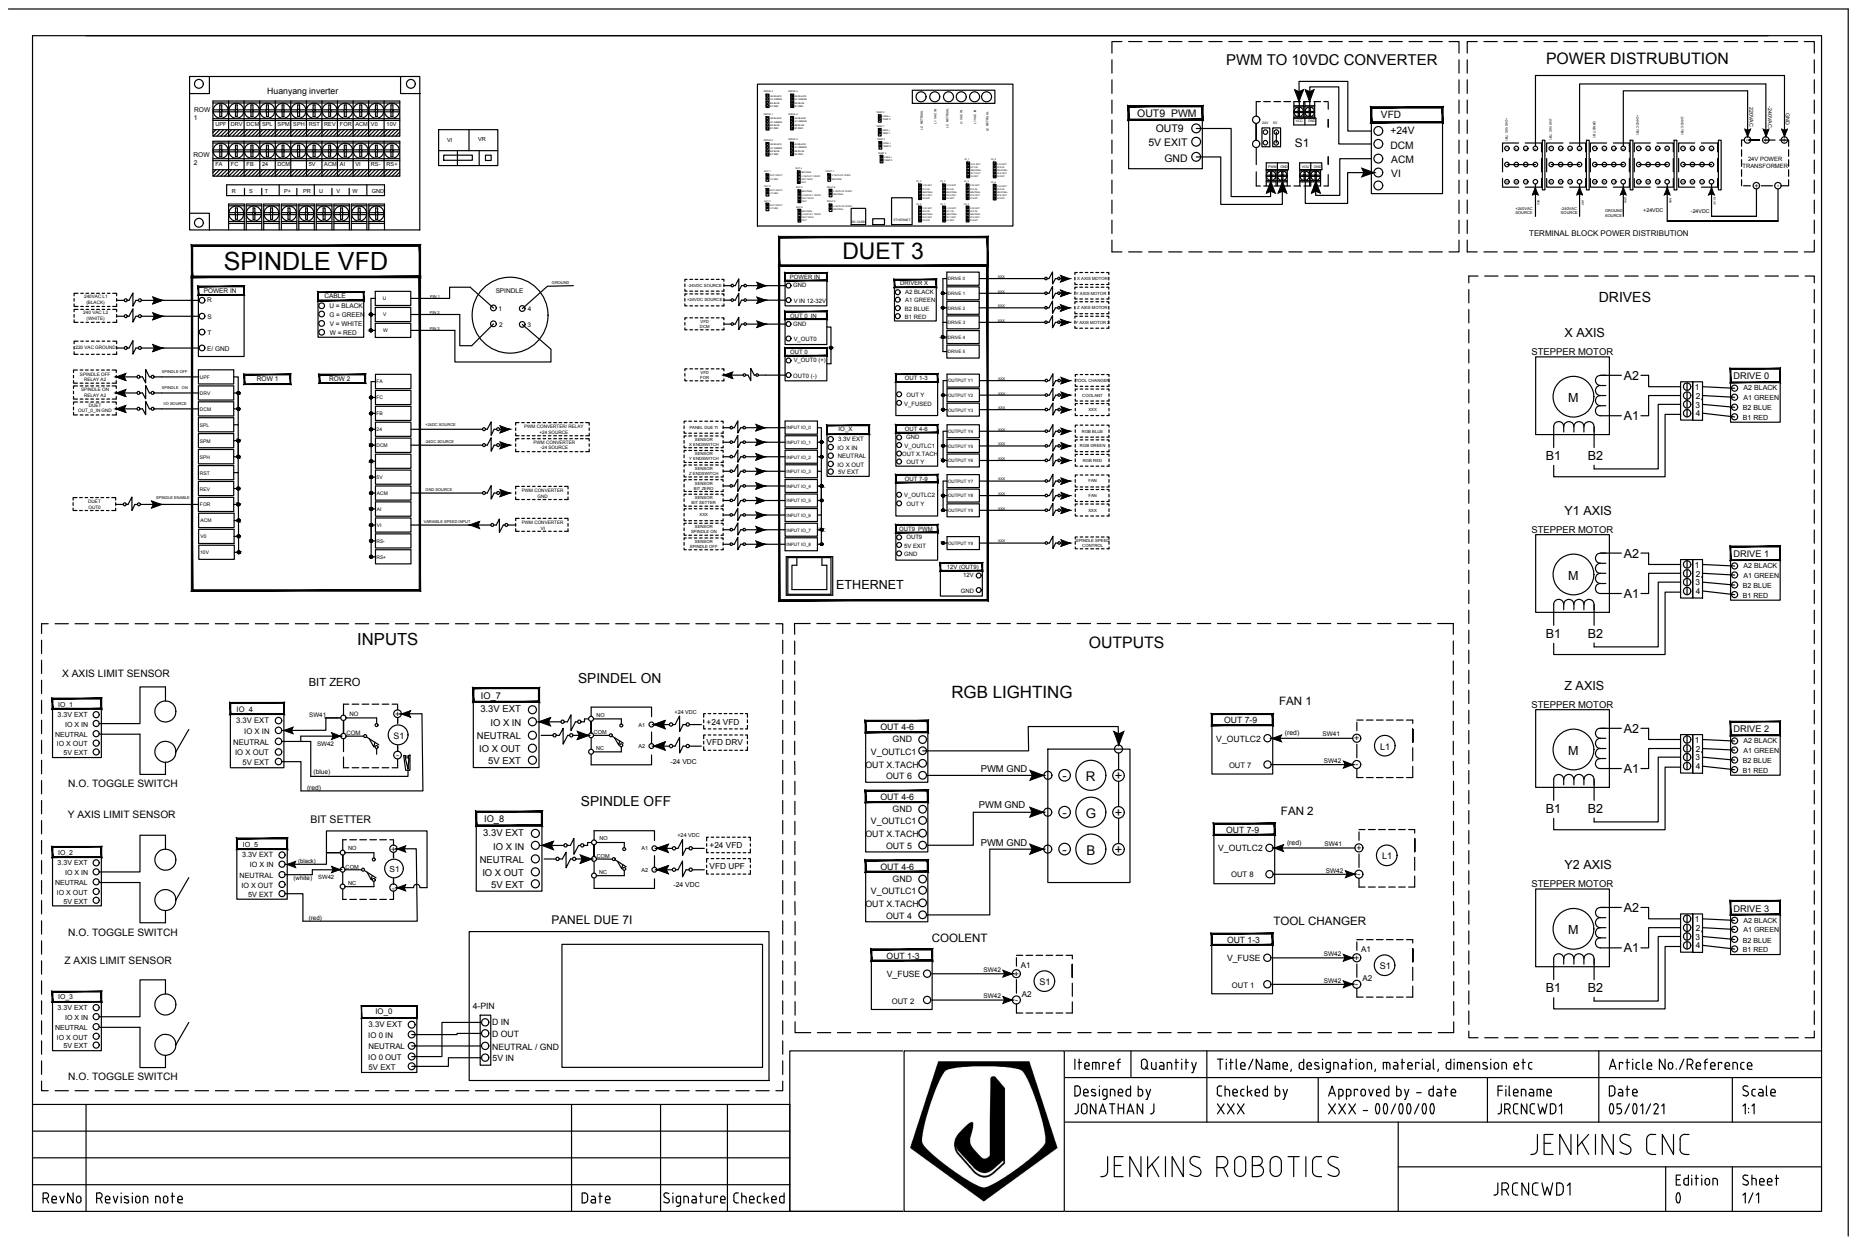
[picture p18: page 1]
A1 GREEN B2 BLUE B1 RED A2 BLACK DRIVE 2; A1 GREEN B2 BLUE B1 RED A2 BLACK DRIVE 3 A1 GREEN B2 BLUE B1 RED A2 BLACK DRIVE 1A1 GREEN B2 BLUE B1 RED A2 BLACK DRIVE 0; A1 GREEN B2 BLUE B1 RED A2 BLACK DRIVE 4A1 GREEN B2 BLUE B1 RED A2 BLACK DRIVE 5OUT 5 OUT 6V OUTLC1 12VDC OUT.TACH OUT NEUTRAL OUT 4 V FUSE OUT VOUT1 OUT 1 OUT 2 OUT 3; NEUTRAL V OUTLC2 12VDC DOUT 7 DOUT 8 DOUT 9; TEMP 0 VSSA + TEMP 1 VSSA + TEMP 1TEMP 2 VSSA + TEMP 2TEMP 3 VSSA + TEMP 3; IO 0 IN NEUTRAL IO 0 OUT 3.3V EXT IO_0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

GND POWER DISTRUBUTION OUTPUTS SPINDLE ENABLE DUET OUT0 SPINDLE VFD ROW 1 UPF DCM DRV SPL SPH SPM RST FOR REV UWV GROUND PIN 1 PIN 2 PIN 3 FAFBFC +24DC SOURCE ROW 2 -24DC SOURCE GND SOURCE G = GREEN V = WHITE W = RED U = BLACK CABLE R S T P+ PR U V W GND Huanyang inverter FA FC FB 24 DCM 5V ACM AI VI RS- RS+ UPF DRV DCM SPL SPM SPH RST REV FOR ACM V0 10V DCM 24 PWM CONVERTER/ RELAY +24 SOURCE PWM CONVERTER -24 SOURCE 5VAI ACM PWM CONVERTER GND RS- VI VARIABLE SPEED INPUT PWM CONVERTER VI V0ACM 10V DUET OUT_0_IN GND RS+ ROW 1ROW 2 POWER IN SR 240VAC L1 (BLACK) T 240 VAC L2 (WHITE) 220 VAC GROUND E/ GND 12 43 SPINDLE I/O SOURCE SPINDLE ON RELAY A2 SPINDLE ON SPINDLE OFF RELAY A2 SPINDLE OFF VI VR INPUTS DRIVES B1 B2 A1A2 M STEPPER MOTOR 1234 A1 GREEN B2 BLUE B1 RED A2 BLACK X AXIS DRIVE 0 B1 B2 A1A2 M STEPPER MOTOR 1234 A1 GREEN B2 BLUE B1 RED A2 BLACK Y1 AXIS DRIVE 1 B1 B2 A1A2 M STEPPER MOTOR 1234 A1 GREEN B2 BLUE B1 RED A2 BLACK Z AXIS DRIVE 2 B1 B2 A1A2 M STEPPER MOTOR 1234 A1 GREEN B2 BLUE B1 RED A2 BLACK Y2 AXIS DRIVE 3 N.O. TOGGLE SWITCH IO X IN NEUTRAL IO X OUT 3.3V EXT 5V EXT Z AXIS LIMIT SENSOR IO_3N.O. TOGGLE SWITCH IO X IN NEUTRAL IO X OUT 3.3V EXT 5V EXT Y AXIS LIMIT SENSOR IO_2N.O. TOGGLE SWITCH IO X IN NEUTRAL IO X OUT 3.3V EXT 5V EXT X AXIS LIMIT SENSOR IO_1 (red) COM SW41 NO SW42 S1+- (blue) IO X IN NEUTRAL IO X OUT 3.3V EXT 5V EXT BIT ZERO IO_4 S1 PWM GND VOUT GND VCC GND 5V EXIT GND OUT9 OUT9 PWM DCM ACM VI +24V 24V 5V PWM TO 10VDC CONVERTER VFD A1A2 V_FUSE SW42 S1 +- SW42 OUT 1-3 TOOL CHANGER OUT 1 A1A2 V_FUSE SW42 S1 +- SW42 OUT 1-3 COOLENT OUT 2 V_OUTLC2 OUT 7-9 (red) SW41 SW42 L1 +- FAN 2 OUT 8 V_OUTLC2 OUT 7-9 (red) SW41 SW42 L1 +- FAN 1 OUT 7 PWM GND - R + - G + - B + V_OUTLC1 OUT X.TACH OUT 6 GND OUT 4-6 V_OUTLC1 OUT X.TACH OUT 5 GND OUT 4-6 V_OUTLC1 OUT X.TACH OUT 4 GND OUT 4-6 PWM GND PWM GND RGB LIGHTING A1A2 +24 VDC NC COM NO -24 VDC IO X IN NEUTRAL IO X OUT 3.3V EXT 5V EXT IO_7 SPINDEL ON +24 VFD VFD DRV A1A2 +24 VDC NC COM NO -24 VDC IO X IN NEUTRAL IO X OUT 3.3V EXT 5V EXT IO_8 SPINDLE OFF +24 VFD VFD UPF (red) COM NO (black) SW42 S1+- (white) IO X IN NEUTRAL IO X OUT 3.3V EXT 5V EXT NC IO_5 BIT SETTER

L1 VAC IN ETHERNET SD CARD IO 1 IN NEUTRAL IO 1 OUT 3.3V EXT 5V EXT IO 2 IN NEUTRAL IO 2 OUT 3.3V EXT 5V EXT IO 5 IN NEUTRAL IO 5 OUT 3.3V EXT 5V EXT IO 4 IN NEUTRAL IO 4 OUT 3.3V EXT 5V EXT IO 3 IN NEUTRAL IO 3 OUT 3.3V EXT 5V EXT IO 6 IN NEUTRAL IO 6 OUT 3.3V EXT 5V EXT IO 8 IN NEUTRAL IO 8 OUT 3.3V EXT 5V EXT IO 7 IN NEUTRAL IO 7 OUT 3.3V EXT 5V EXT NEUTRAL V OUTLC2 12VDC NEUTRAL V OUTLC2 12VDC V FUSE OUT VOUT1 V FUSE OUT VOUT1 V OUTLC1 12VDC OUT.TACH OUT NEUTRAL V OUTLC1 12VDC OUT.TACH OUT NEUTRAL SENSOR SPINDLE OFF SENSOR X ENDSWITCH PANEL DUE 7I SENSOR Y ENDSWITCH SENSOR Z ENDSWITCH DUET 3 IO X IN NEUTRAL IO X OUT 3.3V EXT IO_X 5V EXT INPUT IO_0 INPUT IO_2 INPUT IO_1 INPUT IO_3 INPUT IO_5 INPUT IO_4 INPUT IO_6 INPUT IO_8 INPUT IO_7 SENSOR BIT SETTER SENSOR BIT ZERO XXX SENSOR SPINDLE ON DRIVE 0 DRIVE 2 DRIVE 1 DRIVE 3 XXX X AXIS MOTOR XXX Y AXIS MOTOR 1 XXX Z AXIS MOTOR XXX Y AXIS MOTOR 2 OUTPUT Y1 OUTPUT Y3 OUTPUT Y2 XXX TOOL CHANGER OUT Y V_FUSED OUT 1-3 XXX COOLANT XXX XXX DRIVE 4 DRIVE 5 A1 GREEN B2 BLUE B1 RED A2 BLACK DRIVER X OUTPUT Y4 OUTPUT Y6 OUTPUT Y5 XXX RGB BLUE V_OUTLC1 OUT X.TACH OUT Y GND OUT 4-6 XXX RGB GREEN XXX RGB RED OUTPUT Y7 OUTPUT Y9 OUTPUT Y8 XXX FAN V_OUTLC2 OUT Y OUT 7-9 XXX FAN XXX XXX POWER IN OUT 0 IN OUT0 (-) V_OUT0 (+) OUT 0 5V EXIT GND OUT9 OUT9 PWM OUTPUT Y9 XXX SPINDLE SPEED CONTROL 12V (OUT9) ETHERNET VFD FOR VFD DCM V_OUT0 GND GND 12V V IN 12-32V GND +24VDC SOURCE -24VDC SOURCE 4-PIND OUT NEUTRAL / GND 5V IN D IN PANEL DUE 7I IO 0 IN NEUTRAL IO 0 OUT 3.3V EXT IO_0 5V EXT

-24VDC TB1 TERMINAL BLOCK POWER DISTRIBUTION +24VDC 24V POWER TRANSFORMER +- -24VDC

GRN GROUND SOURCE

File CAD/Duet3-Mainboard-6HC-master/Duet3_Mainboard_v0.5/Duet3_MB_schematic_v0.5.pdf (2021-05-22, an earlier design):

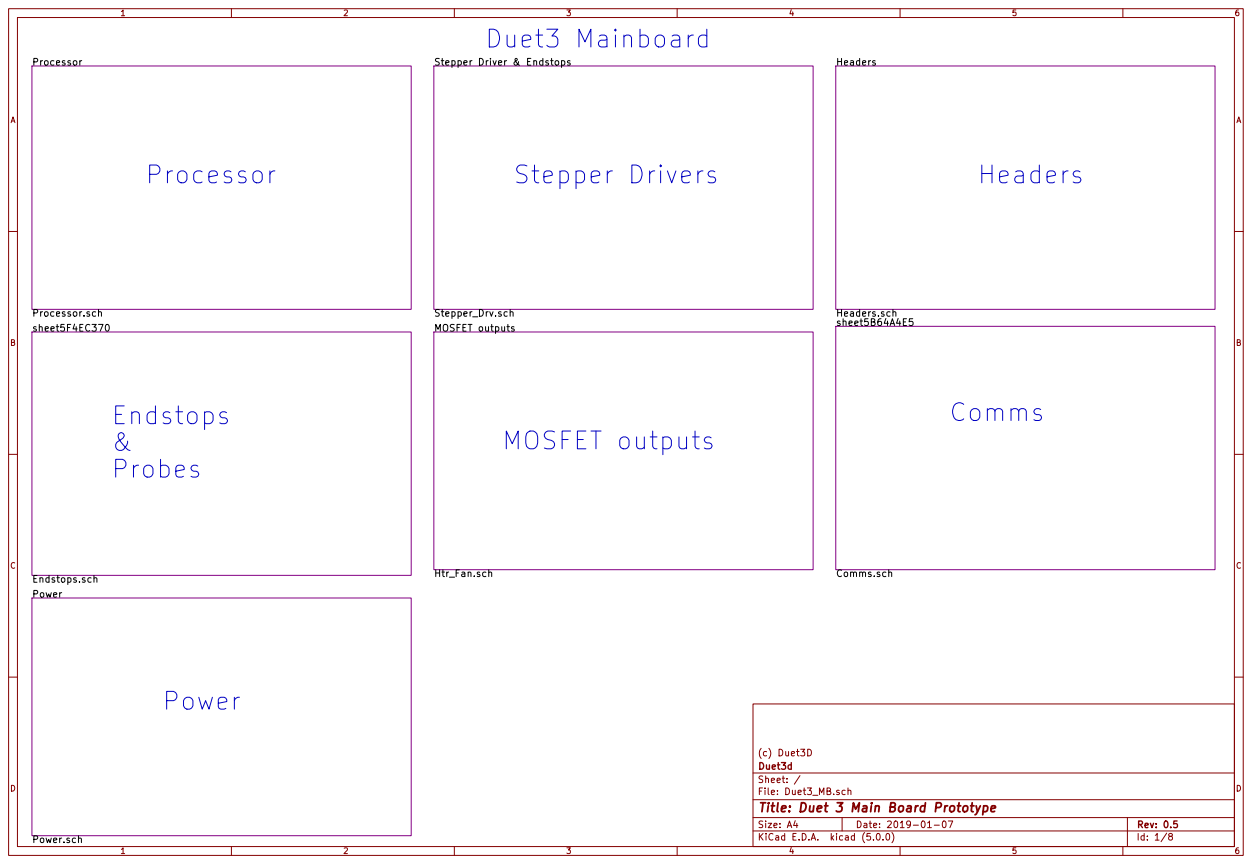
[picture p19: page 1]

Id: 1/8 Title: Duet 3 Main Board Prototype

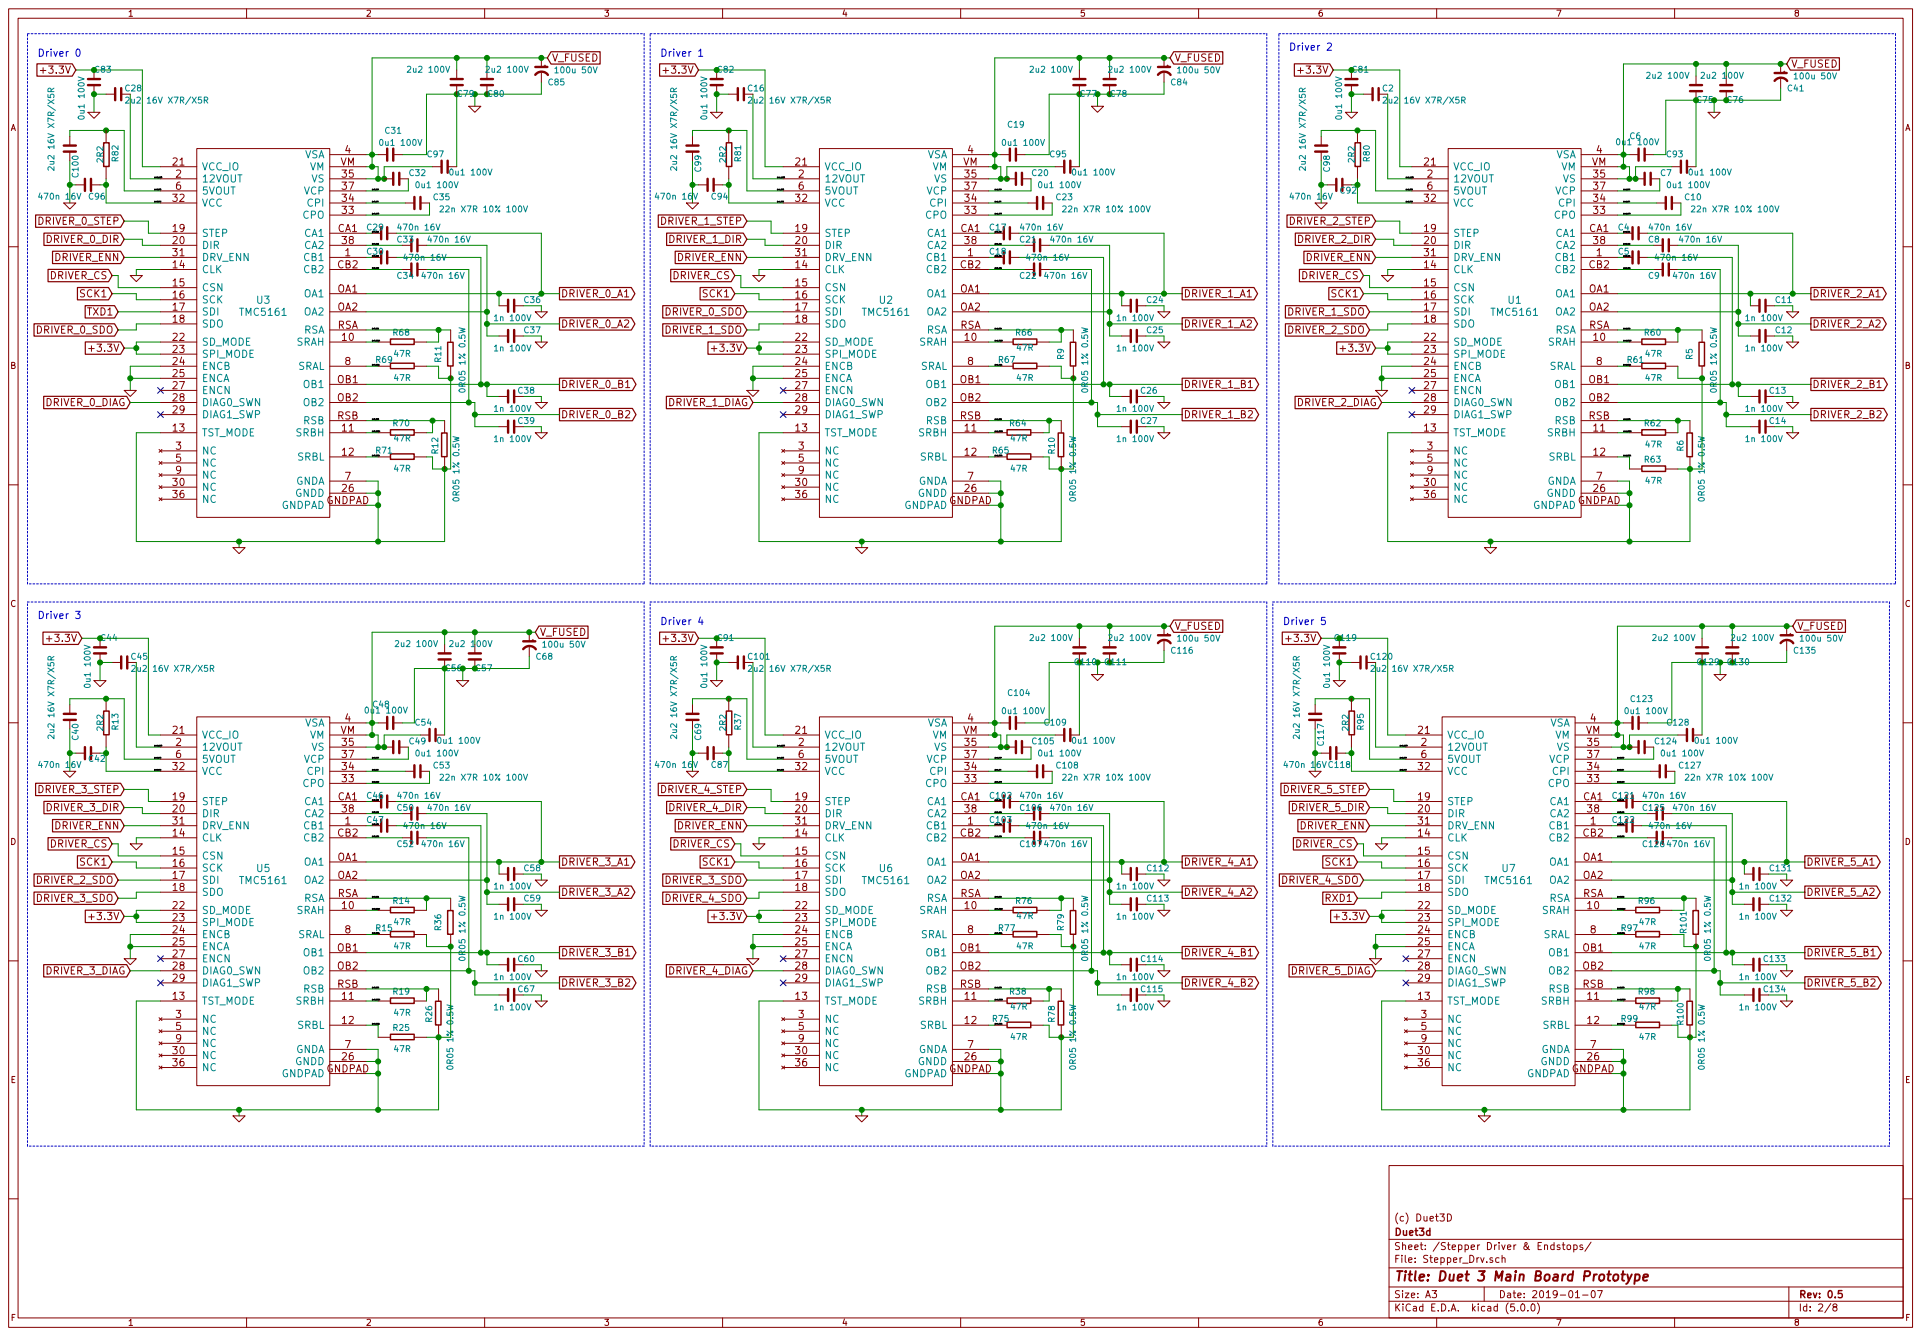
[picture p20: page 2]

(c) Duet3D
Sheet: /Stepper Driver & Endstops/ Duet3d

File: Stepper_Drv.sch
Id: 2/8 Title: Duet 3 Main Board Prototype

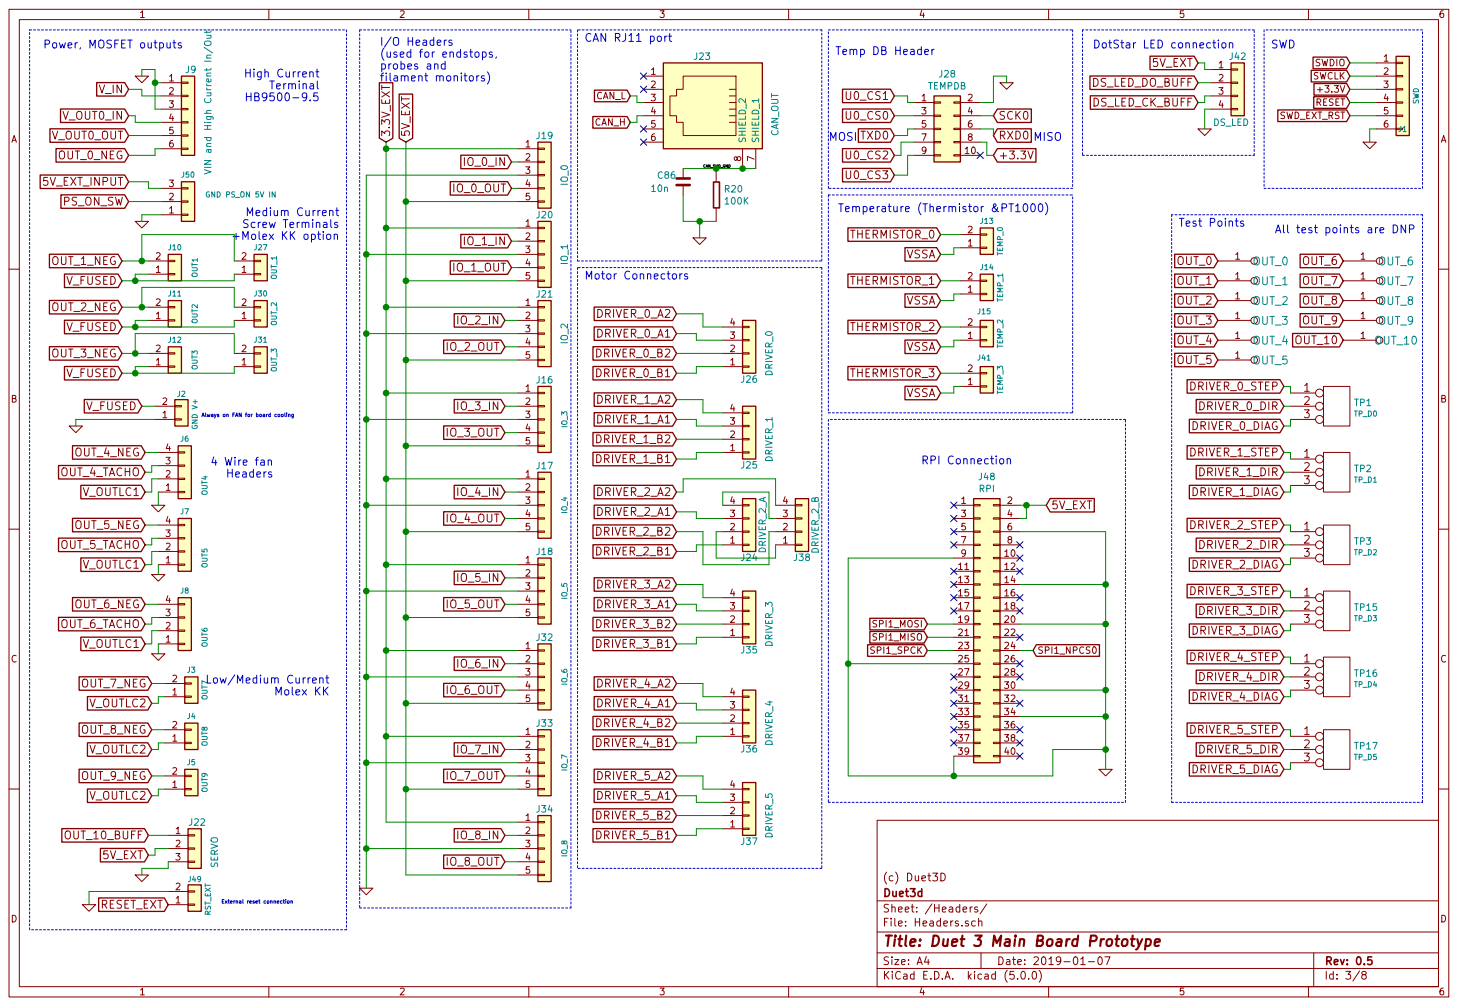
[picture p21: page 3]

All test points are DNP

Always on FAN for board cooling V_OUTLC2

(c) Duet3D
Id: 3/8 Title: Duet 3 Main Board Prototype File: Headers.sch Sheet: /Headers/ Duet3d


2 GND 3 FSW 4 COMP 5 FB 6 SS

5V Input, 3.3V Output for internal use only
Low Drop-Out Linear Regulator

Consider fusing the output Mosfets is groups: Steppers + OUT1-3 = 7.5A/10A OUT4-9 =1A/2A 1

5V Input, 3.3V Output for external use only

CDBA540-HF is overkill, consider using
a cheaper diode when volumes

2 EN 3 ADJ 4 VOUT 5 U18 AP2127K-ADJ C72 1u 16V+ C202 1u 16V+ R180 16K

(c) Duet3D
Id: 4/8 Title: Duet 3 Main Board Prototype File: Power.sch Sheet: /Power/ Duet3d


1N4448WT Some of this reset circuit (e.g the diode)

(c) Duet3D
Id: 5/8 Title: Duet 3 Main Board Prototype File: Processor.sch Sheet: /Processor/ Duet3d


OUT_0_BUFF
Should replace the PMV40UN2 with a higher voltage and potentially higher current MOSFET (gate resistors change depending on FET choice) 1

2 10u caps should be fine
for the three medium power FETs

J29OUT 7- OUT 9 Select V Low current output
Voltage Select

should we have this repeated for banks
of FETS
e.g. OUT 4 -6 (normal fans)

for RC servo control directly GND

File: Htr_Fan.sch
Id: 6/8 Title: Duet 3 Main Board Prototype


CAN Transceiver

there is an internal pull up) Ethernet/Ethercat Master

R130 2 2K2 | 1 D23 USB R121

Note the SAME70xpld uses smaller decoupling caps (4u7, 10u) rather

than the 22u from the PHY datasheet.

3 RXD 4 VIO 5 CANL 6 CANH 7 S

1 MDIO 10 MDC 11 RXD1 12 RXD0 13 VDDIO 14 CRS_RV 15 REF_CLK 16 RXER 17

RD- RD+ TD- TD+ REXTXI XO

J45 SHIELD_GND
shield ground point Do we bother? 1

10K pullup on pin 15 is probably not required (PHY address select,

(c) Duet3D
Id: 7/8 Title: Duet 3 Main Board Prototype File: Comms.sch Sheet: /sheet5B64A4E5/ Duet3d


File: Endstops.sch Sheet: /sheet5F4EC370/ Duet3d

Id: 8/8 Title: Duet 3 Main Board Prototype

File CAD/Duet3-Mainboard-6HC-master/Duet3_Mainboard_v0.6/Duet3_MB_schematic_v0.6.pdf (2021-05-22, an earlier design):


Id: 1/8 Title: Duet 3 Main Board


6 SRAL 7 SRAH 8 SRBH 9 EPAD EPAD U1 TMC5160

6 SRAL 7 SRAH 8 SRBH 9 EPAD EPAD U2 TMC5160

6 SRAL 7 SRAH 8 SRBH 9 EPAD EPAD U5 TMC5160

6 SRAL 7 SRAH 8 SRBH 9 EPAD EPAD U6 TMC5160

(c) Duet3D
Sheet: /Stepper Driver & Endstops/ Duet3d

File: Stepper_Drv.sch
Id: 2/8 Title: Duet 3 Main Board


J9 VIN and High Current In/Out OUT_0_NEG

All test points are DNP

Always on FAN for board cooling V_OUTLC2
V_FUSED

(c) Duet3D
File: Headers.sch Sheet: /Headers/ Duet3d

Id: 3/8 Title: Duet 3 Main Board


2 GND 3 FSW 4 COMP 5 FB 6 SS

JP4 is normally fitted:
Duet powers SBC
JP5 allows for SBC to Power Duet. Bypasses 5V protection

5V Input, 3.3V Output for internal use only
Low Drop-Out Linear Regulator

Consider fusing the output Mosfets is groups: Steppers + OUT1-3 = 7.5A/10A OUT4-9 =1A/2A R164

5V Input, 3.3V Output for external use only

2 EN 3 ADJ 4 VOUT 5 U18 AP2127K-ADJ C72 1u 10V+ C202 1u 10V+ R180 16K R181 5K1

(c) Duet3D
File: Power.sch Sheet: /Power/ Duet3d

Id: 4/8 Title: Duet 3 Main Board


Pulldown on Driver 0 DIR

1N4448WT Some of this reset circuit (e.g the diode)

(c) Duet3D
File: Processor.sch Sheet: /Processor/ Duet3d

Id: 5/8 Title: Duet 3 Main Board


2 10u caps should be fine
for the three medium power FETs

J29OUT 7- OUT 9 Select V Low current output
Voltage Select

File: Htr_Fan.sch
Id: 6/8 Title: Duet 3 Main Board


CAN1 Transceiver

the default is fine). Ethernet/Ethercat Master

R130 2 2K2 | 1 D23 USB R121

Note the SAME70xpld uses smaller decoupling caps (4u7, 10u) rather

than the 22u from the PHY datasheet.

3 RXD 4 VIO 5 CANL 6 CANH 7 S

1 MDIO 10 MDC 11 RXD1 12 RXD0 13 VDDIO 14 CRS_RV 15 REF_CLK 16 RXER 17

RD- RD+ TD- TD+ REXTXI XO

10K pullup on pin 15 is probably not required (PHY address select,

(c) Duet3D
File: Comms.sch Sheet: /sheet5B64A4E5/ Duet3d

Id: 7/8 Title: Duet 3 Main Board


File: Endstops.sch Sheet: /sheet5F4EC370/ Duet3d

Id: 8/8 Title: Duet 3 Main Board

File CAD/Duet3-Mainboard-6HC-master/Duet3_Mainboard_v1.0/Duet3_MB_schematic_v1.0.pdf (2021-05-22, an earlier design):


Sheet: Headers File: Headers.sch Sheet: Power File: Power.sch

Sheet: Stepper Driver & Endstops

Id: 1/8 Title: Duet 3 Main Board


6 SRAL 7 SRAH 8 SRBH 9 EPAD EPAD U5 TMC5160 C6 2u2 R62

6 SRAL 7 SRAH 8 SRBH 9 EPAD EPAD U1 TMC5160 C5 2u2 C9

6 SRAL 7 SRAH 8 SRBH 9 EPAD EPAD U6 TMC5160

(c) Duet3D
Sheet: /Stepper Driver & Endstops/ Duet3d

File: Stepper_Drv.sch
Id: 2/8 Title: Duet 3 Main Board


High Current Terminal HB9500-9.5 Medium Current

IO_2_OUT
4 Wire fan Headers Low/Medium Current Molex KK

Always on FAN for board cooling

additional 12V supply if a VFD convertor is used

(c) Duet3D
File: Headers.sch Sheet: /Headers/ Duet3d

Id: 3/8 Title: Duet 3 Main Board


SBC <-> Duet 5V jumpers Mini Blade Fuses

2 EN 3 ADJ 4 VOUT 5 U18 AP2127K-ADJ R105 47K R104 10K

2 GND 3 FSW 4 COMP 5 FB 6 SS

JP5 allows for SBC to Power Duet. Bypasses 5V protection

Low Drop-Out Linear Regulator

5V Input, 3.3V Output for external use only

Consider fusing the output Mosfets is groups: Steppers + OUT1-3 = 7.5A/10A OUT4-9 =1A/2A

(c) Duet3D
File: Power.sch Sheet: /Power/ Duet3d

Id: 4/8 Title: Duet 3 Main Board


VREFP may need additional filtering?
THERMISTOR_2 VREFP
THERMISTOR_0VSSA_MON VSSA

Pulldown on Driver 0 DIR
ID this as a v0.6 board
IO_1_OUT DRIVER_0_DIR

Tacho Pullups & Series Resistors

Some of this reset circuit (e.g the diode)

(c) Duet3D
File: Processor.sch Sheet: /Processor/ Duet3d

Id: 5/8 Title: Duet 3 Main Board


OUT 1 MOSFET CONTROL FET Drives

2 10u caps should be fine
for the three medium power FETs

File: Htr_Fan.sch
Id: 6/8 Title: Duet 3 Main Board


the default is fine). CAN1 Transceiver

shield ground point USB

than the 22u from the PHY datasheet. Ethernet/Ethercat Master

Note the SAME70xpld uses smaller decoupling caps (4u7, 10u) rather

3 RXD 4 VIO 5 CANL 6 CANH 7 S

1 MDIO 10 MDC 11 RXD1 12 RXD0 13 VDDIO 14 CRS_RV 15 REF_CLK 16 RXER 17

Off board termination
resistors required for CAN0 bus.
Alternative solder 120 Ohm
1206 resistor to the DNP pads at the bottom of the board

(c) Duet3D
File: Comms.sch Sheet: /sheet5B64A4E5/ Duet3d

Id: 7/8 Title: Duet 3 Main Board


IO inputs (Used for endstops, probes, filament monitors and other low speed IO)

(c) Duet3D
File: Endstops.sch Sheet: /sheet5F4EC370/ Duet3d

Id: 8/8 Title: Duet 3 Main Board

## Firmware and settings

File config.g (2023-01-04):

conf
; Configuration file for Duet 3  FIRMWARE RepRapFirmware 3.3 and later
; executed by the firmware on start-up
; Generated referencing RepRapFirmware Configuration Tool v3.1.8 and WorkBee Firmware Version 1.0.7

;JenkinsCNC v1.2
;Updated 7.13.21
;Board: Duet 3
;Firmware: Reprap Firmware 3.3 and later



; General preferences
M453 					                ; Put the machine into CNC Modes
M550 P"JenkinsCNC"                      ; set printer name
G90 					                ; Set absolute coordinates
G21 					                ; Set units to mm


; Network
M552 P192.168.86.64 S1                  ; enable network and set IP address
M553 P255.255.255.0                     ; set netmask
M554 P192.168.86.1                      ; set gateway
M586 P0 S1 				                ; Enable HTTP
M586 P1 S0 				                ; Disable FTP
M586 P2 S0 				                ; Disable Telnet

; Configure Drives
M569 P0.0 S0 				            ; Physical drive 0.0 direction (0 = backwards, 1 = forwards (default 1))
M569 P0.1 S1 				            ; Physical drive 0.1 direction (0 = backwards, 1 = forwards (default 1))
M569 P0.2 S0 				            ; Physical drive 0.2 direction (0 = backwards, 1 = forwards (default 1))
M569 P0.3 S0 				            ; Physical drive 0.3 direction (0 = backwards, 1 = forwards (default 1))
M584 X0.0 Y0.1:0.3 Z0.2 	            ; Apply drive mapping to axes - dual Y axis

; Configure Axes
M92 X80 Y80 Z400 				        ; Set steps per mm
M350 X16 Y16 Z16 I1 			        ; Configure microstepping
M566 X500 Y500 Z500 			        ; Set maximum instantaneous speed changes (mm/min)
M203 X5000 Y5000 Z5000 		            ; Set maximum speeds (mm/min)
M201 X400 Y400 Z400				        ; Set accelerations (mm/s^2)
M906 X2400 Y2400 Z2400 I100 		    ; Set motor currents (mA)

; Configure Axis Limits
M208 X-838 Y-838 Z-85 S1 		        ; Set axis minima  ( 0 = set axis maximum (default), 1 = set axis minimum)
M208 X0 Y0 Z0 S0            		    ; set axis maxima  ( 0 = set axis maximum (default), 1 = set axis minimum)

; Configure IO / Endstops
M574 X2 S1 P"!io1.in"                   ; configure active-high endstop for high end on X via pin !io1.in ( 0 = none, 1 = low end, 2 = high end)
M574 Y2 S1 P"!io2.in"                   ; configure active-high endstop for high end on Y via pin !io2.in
M574 Z2 S1 P"!io3.in"                   ; configure active-high endstop for high end on Z via pin !io3.in

; Configure IO / Probes
M558 K1 P8 C"!io4.in" H5 F100 T3000 	; XYZ Workpeice probe (bitzero) connected to io4 input
M558 K2 P8 C"!io5.in" H5 F500 T3000 	; TOOL Z probe (bitsetter)  connected to io5 input
G31 Z0 ; Set Z probe trigger height

; CNC INPUTS
M950 J1 C"!io7.in"                         ; create input pin 1 on pin io7.in (Spindle on & At rpm) 
M950 J2 C"!io8.in"                         ; create input pin 2 on pin io8.in (Spindle Stopped) 

; CNC OUTPUTS SPINDLE
M950 R0 C"out9+out0" L0:24000 			; Create spindle index 0, with PWM pin on OUT 9  and Supports range 0-2400 RPM


; CNC OUTPUTS
M950 P1 C"out1"                         ; create io 1 on pin out1 (TOOL CHANGER) 
M950 P2 C"out2"                         ; create io 2 on pin out2 (COOLENT)
M950 P4 C"out4"                         ; create io 4 on pin out4 (RGB LIGHTING : BLUE)
M950 P5 C"out5"                         ; create io 5 on pin out5 (RGB LIGHTING : GREEN)
M950 P6 C"out6"                         ; create io 6 on pin out6 (RGB LIGHTING : RED)
M950 F7 C"out7" Q500                    ; create fan 7 on pin out7 and set its frequency (FAN)
M950 F8 C"out8" Q500                    ; create fan 8 on pin out8 and set its frequency (FAN)



; Tools
M563 P1 S"tool1" R0                     ; define tool 1 with spindle 0 
G10 P1 X0 Y0 Z0                         ; set tool 1 axis offsets
M563 P2 S"tool2" R0                     ; define tool 2 with spindle 0 
G10 P2 X0 Y0 Z0                         ; set tool 2 axis offsets
M563 P3 S"tool3" R0                     ; define tool 3 with spindle 0 
G10 P3 X0 Y0 Z0                         ; set tool 3 axis offsets
M563 P4 S"tool4" R0                     ; define tool 4 with spindle 0 
G10 P4 X0 Y0 Z0                         ; set tool 4 axis offsets
M563 P5 S"tool5" R0                     ; define tool 5 with spindle 0 
G10 P5 X0 Y0 Z0                         ; set tool 5 axis offsets
M563 P6 s"tool6" R0   	            	; define tool 6 with spindle 0 
G10 P6 X0 Y0 Z0            				; set tool 6 axis offsets
;M568 P60 F24000                           ; set spindle RPM for tool 6)



; Other Settings
M575 P1 S1 B57600                       ; enable support for PanelDue
M140 H-1								; Disable heated bed
M564 S1 H1 								; Disable jog commands when not homed
M911 S21.0 R23 P"G91 G1 Z3 F1000" 		; Configure power loss resume
M501									; Load Stored Parameters 
M98 P"lighthome.g"						; set red light

; initial setup
M577 P2									; Wait Until the Input 2 is High (SPINDLE STOP FROM VFD)
M5                                      ; STOP SPINDLE
;M106 P0 S0                              ; turn off fan 0 (SPINDLE ENABLE) (RANGE : 0 to 255 or 0.0 to 1.0)
M42 P1 S0                   			; turn ON fan 1 (TOOL CHANGER Locked) (RANGE : 0 to 255 or 0.0 to 1.0)  
M42 P2 S0.0           					; turn off Output # 2 (Dust Collector) (RANGE : 0 to 255 or 0.0 to 1.0) 
M106 P7 S0                              ; turn off fan 7 (fan) (RANGE : 0 to 255 or 0.0 to 1.0) 
M106 P8 S0                              ; turn off fan 8 (fan) (RANGE : 0 to 255 or 0.0 to 1.0) 
G28			          					; Home all Axis
M98 P"lighton.g"						; set WHITE light

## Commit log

2021-05-25 update wire diagram
    [JRCNCWD1.dwg]
2021-06-29 File Management
    Updated Files
    [DUET CNC 2.0.dwg, DUET CNC 3.0.dwg]
2021-07-17 Release 2.0
    Updated Project file for the use of the new Pneumatic Dust Shoe for the ATC.
    Updated bug fixes for post processor, and variety of gcode macros.
    Updated Duet 3 to Reprap 3.3
    [ZProbe.g, config-override.g, config.g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]
2021-07-18 Missing file
    uploaded missing workzero.g file
    [workzero.g]
2021-08-14 ZProbe
    Updated Zprobe to support a fast probe follower by a slow probe
    [bed.g, cancel.g, config-override.g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]
2022-08-31 CAD Upload
    Uploaded cad files
    [JRCNC0001 v12.f3d, JRCNC0002 v2.f3d, JRCNC0006 v3.f3d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]
2023-01-04 Upload for Release 3.0
    New Macros, New Folders, New CAD, New Post Processor
    https://github.com/JenkinsRobotics/JenkinsCNCPostProcessor/releases/tag/V2.0
    [DUET CNC 2.0.dwg, DUET CNC 3.0.dwg, JRCNCWD1.dwg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]
2023-01-04 Release 3.0
    [DUET CNC 2.0.dwg, DUET CNC 3.0.dwg, JRCNCWD1.dwg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]
